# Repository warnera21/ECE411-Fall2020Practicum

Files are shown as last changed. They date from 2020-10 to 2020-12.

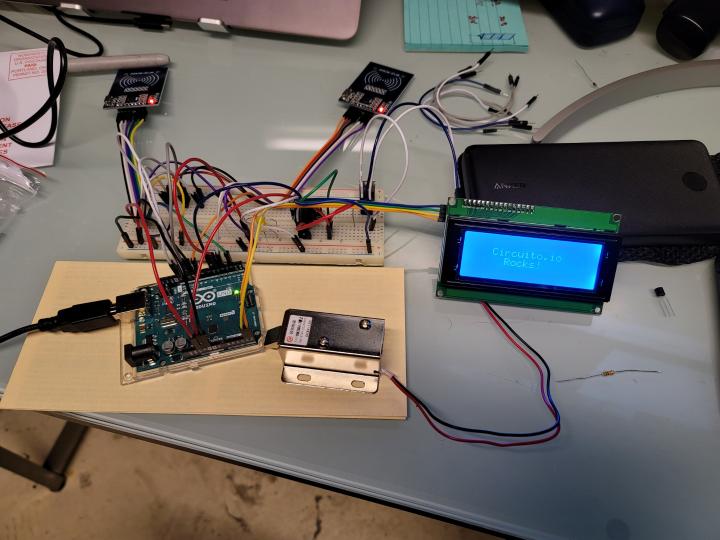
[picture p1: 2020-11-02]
Status Reports/Nov 2 2020 HW4 Picture.jpg

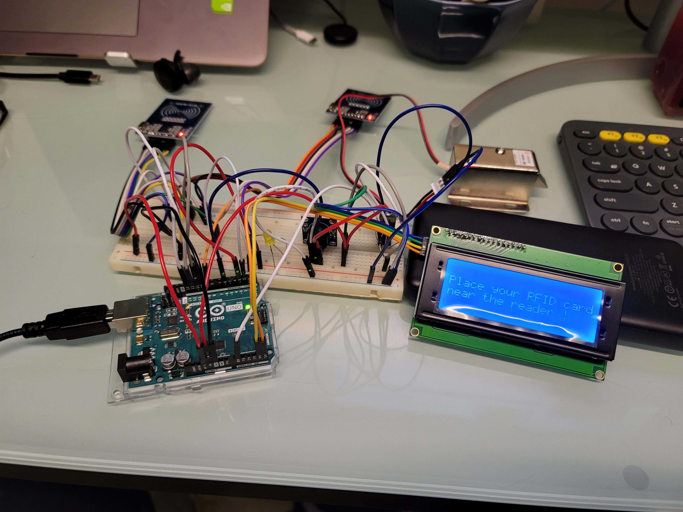
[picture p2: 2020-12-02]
breadboard- team 8.jpg

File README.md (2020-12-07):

# ECE411-Fall2020Practicum
This project is based in adding security and ease of access trough a door using Facial Recognition and RFID technologies. The implementation of keeping track of how many (Authorized) user go inside/out of a building is an extra feature that can aid with companies enforcing distancing strategies for COVID purposes. 

### TEAM 8: Hamed AlSaegui, Anthony Warner, Josh Pradera and Tamar Stigler-Flores.

### Arduino Code

	==> if the code is not uploaded yet
		the file (411.ino) must be inside a folder named (411)
		Follow the ... for board connections
		compile and upload the programm to the ATMega chip.
		
	==> used libraries
		SPI.h
		MFRC522.h
		LiquidCrystal_I2C.h
		Wire.h
	==> High Level Diagram Code
		set the LCD address to 0x27 for a 16 chars and 2 line display
		initialize the lcd
		initialize counter
		initialize receiveEvent function
			receive byte as a character
		VOID SETUP
			Initiate I2C communication
			Initiate  address bus designated to I2C with Raspberry Pi
			Initiate each MFRC522 card
			Join I2C bus as slave with address 8
				Call receiveEvent when data received 
			initialize output pins
		VOID LOOP
			be ready to scan a tag
				if scanned to ENTER (RFID1)
					If Tag is Valid
						AUTHORIZED
					If Tag is Not Valid
						UNAUTHORIZED
				if scanned to EXIT (RFID2)
					If Tag is Valid
						AUTHORIZED
					If Tag is Not Valid
						UNAUTHORIZED

### Raspberry Pi Code (Python Script)

	==> The sequence of the Face Recognition code goes as follow:
		1 - Collect the data set of pictures from each user.
		==> Used libraries: 
		    cv2 (openCV)
		    numpy
		 ==> Use the CascadeClassifier and load haarcascade_frontal_default.xml (used for the detection of faces)
		     Setup the raspberry pi camera
		     Setup input variable to assign an specific User ID (as a number)
		     WHILE TRUE
		     		Read from the raspberry pi camera.
				Set a onvertion for the photos from RGB to Gray Scale.
				Detect the face from the user.
				Increase the sampleNum variable by 1 as the picture samples are taken.
				Open window with video feed and also draw a rectangle on the detected face.
				Save 20 pictures in a folder named dataSet.
				When done break the LOOP.
		    Release the camera.
		    Destroy all the windows opened by the program.
		    
		    2- Train the data and create a file named trainingData.yml that will be used to recognize an user.
		       The .yml file contains  the serialized data for specific users.
		   ==> Used libraries:
		       os 
		       cv2
		       numpy
		       from PIL import Image (for manipulation of Images)
		       Create variable recognizer and call the function to create a Local Binary Operator.
		       	-  LBPH is used to extract features from an input image and match them with the faces in system's database.
		       Set the dataSet path.
		       Create  two arrays. One name faces and another names IDs.
		      		 Execute a for loop that will loop as many times as the amount of images that we have in the dataSet folder.
		      		 Convert images in monochromo format.
		      		 Convert images into a numpy array with name faceImg.
		      		 Extract ID from the name of the image and add it to the array IDs and add the data to the array faces.
		       Train the data set.
		       Save the .yml file inside recognizer folder.
		       Destroy all the windows opened by the program.
		       
		    3- Recognize a face an open the door.
		    ==> Used libraries:
		        numpy
			cv2
			time
			from smbus import SMBus (I2C communication)
		        Specify bus address used for I2C.
			Setup the CascadeClassifier function with the haarcascade_frontalface_default.xml
			Setup Raspberry Pi camera.
			Create a variable named rec and use the Local Binary Operator function.
			Load the trained data present in the .yml file.
			Initiate id to 0
			Create a solenoid function for the I2C communication between Raspberry Pi and Arduino.
				Write a byte 0x1 using bus address 0x8 to unlock the door.
				Wait for 5 seconds.
				Write a byte 0x0 using the same bus address  to Lock the door.
				
			While True
				Read from Raspberry Pi camera.
				Convert pictures from Color to Gray Scale.
				Set a Multiscale to compensate from faces closer and far away from the camera.
			        For LOOP 
					Start the prediction of the user based in the trained data and the face detected using the haar cascade file.
					Compare faces detected to IDs .
					If the ID and face detected match, release the camera and set the camera again for stability issues with the time library.
						Print the user Name in the terminal for testing purposes.
						Call the solenoid function and send  a 0x1 bit to the Arduino over I2C to unlock door.
						Wait for 5 seconds. 
						Send  a 0x0 bit to the Arduino to lock the door.
					ELSE IF ID dosnt match the trained data set.
						Print Unauthorized user in the terminal for testing purposes.
						Release the camera.
						Setup the camera. 
						
				Brake out of the program with cntrl+C. 
				Release the camera.
				Destroy all the windows created by the program.

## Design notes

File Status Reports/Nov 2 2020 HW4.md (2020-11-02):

Status Report - Nov 2 2020

Our breadboard is running one RFID reader correctly to read and verify the RFID Cards. The I2C LCD is connected and displays the
correct output to the user when "Access Denied" or "Authorized access." We have a yellow LED to also be another verification for the 
user to know if they are granted access. For now, we are having some issues with the second RFID reader and need to get the correct 
power supply for the solenoid to work with the breadboard setup.

A video of our breadboard working is on youtube at this link [RFID and Facial Recognition](https://youtu.be/yJKnMJHlXBU)

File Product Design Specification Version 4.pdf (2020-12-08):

12/07/2020 | Version 4

ECE411
Product Design Specifications PDS

### Facial Recognition Smart Door Lock

TEAM #8
Tamarr Stigler
Hamed AlSaeghi
Josh Pradera
Anthony Warner

12/06/2020 | Version 3

Introduction

This project consists of a Facial Recognition Smart Door Lock using RFID and Facial Recognition technology. RFID is known as the radio frequency identification, using electromagnetic fields to automatically identify tags that can be placed in many things. A part of this project is to use RFID cards to grant access to users entering and exiting a door. The system can also help in tracking the number of people existing inside the place as well as updating itself as users exit a door. There will be two sets of LEDs, a pair for the entrance signifying granted access and denied access and another set for the exiting also to communicate granted or unauthorized exit. The reason we want to grant authorized and unauthorized exiting is because the system will keep track of how many people in the building remain from the RFID door lock. There will be an LCD display that will show “Authorized Access!” when the user is recognized either by the face detection mode or by using the RFID , “Unauthorized access!” only when using the wrong RFID card.
In the case of the facial recognition section a user that is unauthorized to access will not trigger the opening of the door . Another part of the project is the use of Facial recognition from the user. We will be using a camera connected to a raspberry pi with the addition of openCV. The raspberry pi will communicate with the Atmega328 board via I2C (SDA and SCL pins) allowing the Atmega328 to trigger a solenoid lock and granting access to the user. It needs to recognize your face for approval. The objective of this project is to access a door having two options RFID and Facial Recognition. This system adds a layer of security to a door lock that can be implemented in any place, that be for the ease to enter a place without a key or for the added security introduced with RFID and Facial recognition.

Needs Statement

- A Facial Recognition Smart Door Lock is needed to provide users with more secure access to their properties.

Objectives Statement

- The objective of this project is to design and prototype a device that will make accessing properties safer by providing two authentication methods to unlock a door.

Market Analysis

This is intended towards any customers. We want to ensure it is useful for any security purposes. One way it could be used would be for homeland security. Another way it could be used is Business companies or corporations. Any Revences could use this as well.

Good ideas come with good competition. Common things facial recognition are used for are cellular phones and tablets. Currently Samsung and Iphones installed facial recognition for users and they used it as an authentication method to get permission. Same for some basic locks that follow the same methodology to provide access to a property. However, our product for the smart door will be providing much safer access to a property; it will not only scan your face, it also uses the tags scanning method as another authentication step with the potential of having it count the number of people entering and leaving with timings and push to a server to analyze it. We are planning to sell this product at $399.99. This price covers a profit since the value has been doubled.

Requirements

MUST
- Take a face as an input.
- Take an ID Tag as another input .
- Output for opening or not-opening the door.
- Has a visual interface for the user.
- Has at least 5 seconds between each output.
- Safe to use by non-engineers.
- Consistently recognize a face.
- Has an indicators to indicate access authorized/denied

SHOULD
- Not use batteries.
- Cost less than $300 to design.
- Always be running.
- Has two input options for Entering.
- Has one input option for Exiting.

MAY
- Has an interface with more than one language.
- Be able to do some statistical analysis.
- Be able to push statistics to a server and analyze it.
- Be able to register new users.

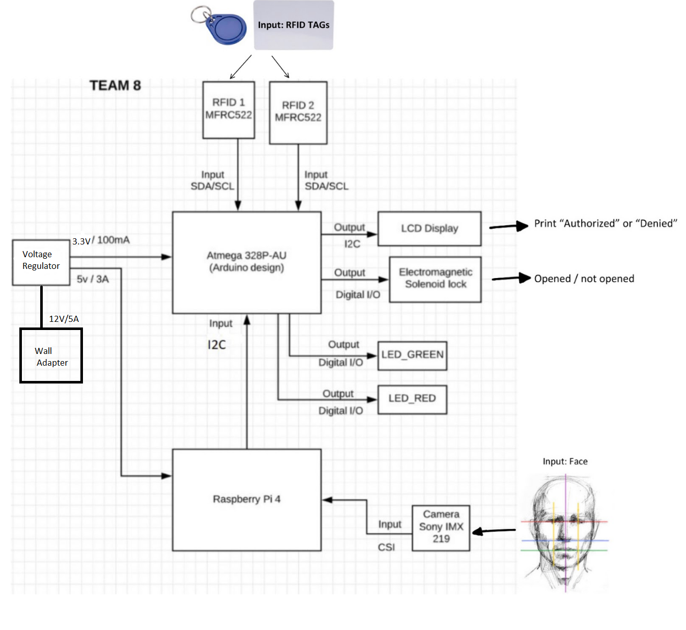
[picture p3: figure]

Design Specifications

- Raspberry PI 4 (4 GB).
- Atmega328-Au (Arduino Design).
- Wall adapter capable of 12V 5A.
- 6v 1.5A 11.4 mm Electromagnetic Solenoid Lock Assembly.
- Step up/down buck converter.
- Two RFID RC522 Module IC Car Reader Read RF Proximity Sensor.
- Raspberry Pi Noir Camera Module V2 8MP 1080p.
- LCD display Module 5v 20x4 Character LCM Blue Backlight.
- 2xRed Led and 2xGreen Led.
- Four 1kOhm resistors for the leds.
- Level Shifter.
- SD card.
- Stemedu RFID RC522 Module IC Card Reader Read RF Proximity Sensor ●

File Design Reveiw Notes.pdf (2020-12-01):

ECE411
PEER DESIGN REVIEW
TEAM 8

TEAM 8:
- Tamarr Stigler-Flores
- Anthony Warner
- Hamed AlSaeghi
- Josh Perdera

TEAM 16:
- Ahmad Alothaimin
- Nathan Paul
- Jakob White
- James Ross

SCHEMATIC NOTES:

- Remove supply diode.
- Remove 3.3v supply for raspberry pi
- Usbvcc will explode usb chip
- Diode OR connections (5v supply and usbvcc)
- DC plug connect to ground pins 2 and 3
- 4.7k pull-up 5v for LCD I2C
- 1k resistor for LEDs
- 100nF capacitor connection to gnd from USB shield
- Remove Q1 and R4
- S1 Switch:
Having (1 and 2) connecting in parallel and (3 and 4) in parallel. Isn’t this supposed to cause some issues ?
- Solenoid lock and other sensors:
Better to have them in separate blocks
- Having labels
Better to connect with wires rather than labels
- AREF
What is it? What does it do?

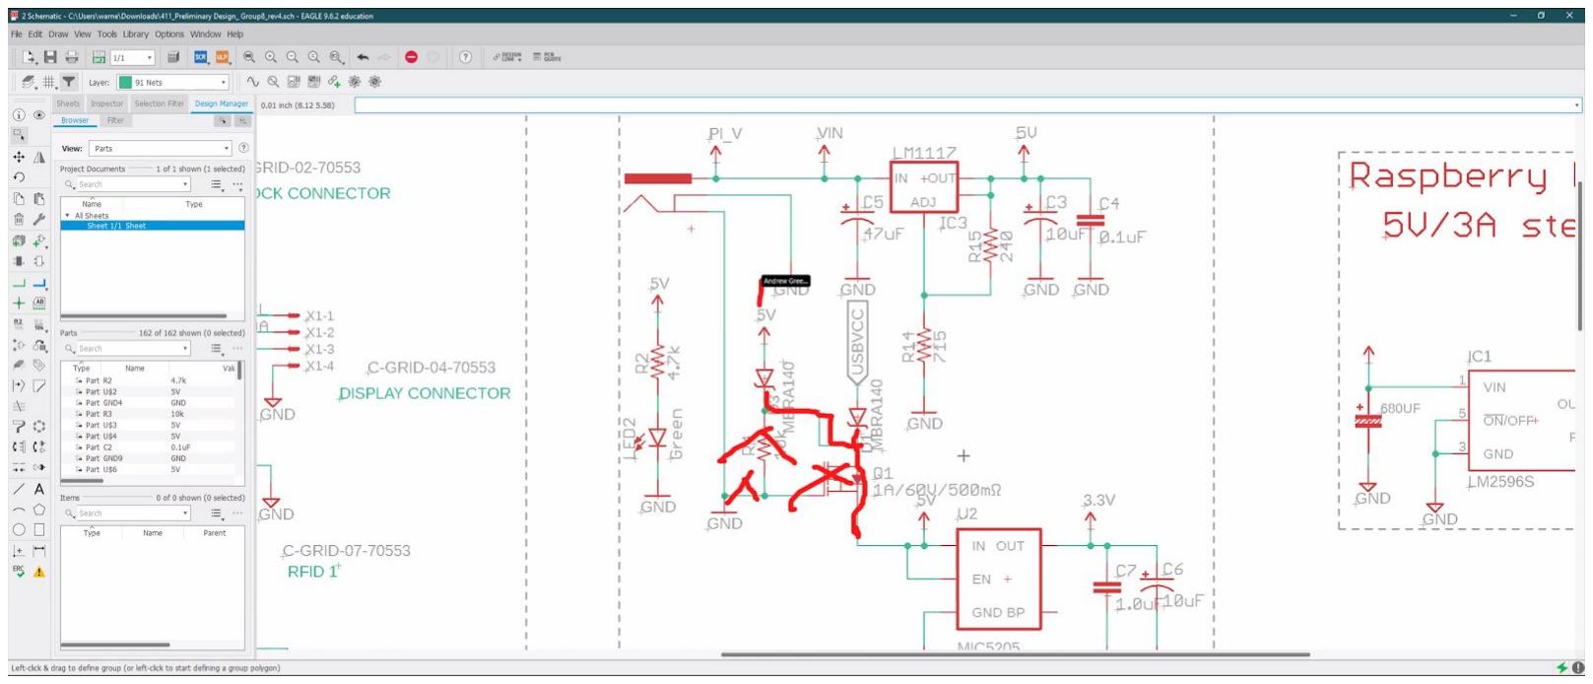
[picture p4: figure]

BOARD NOTES:

- More test points
- Gnd plane
- Test points
- Wider traces
- Board outline skewed
- Flood the gnd plane first
- Group switching power supply on board
- Thick lines on switching power supply
- Placement of mini usb
- Make the silk screen larger print
- Minimum trace size is 12mil for data lines and 50mil for power lines
- Add labels to test points
- Add more ground vias in open spaces

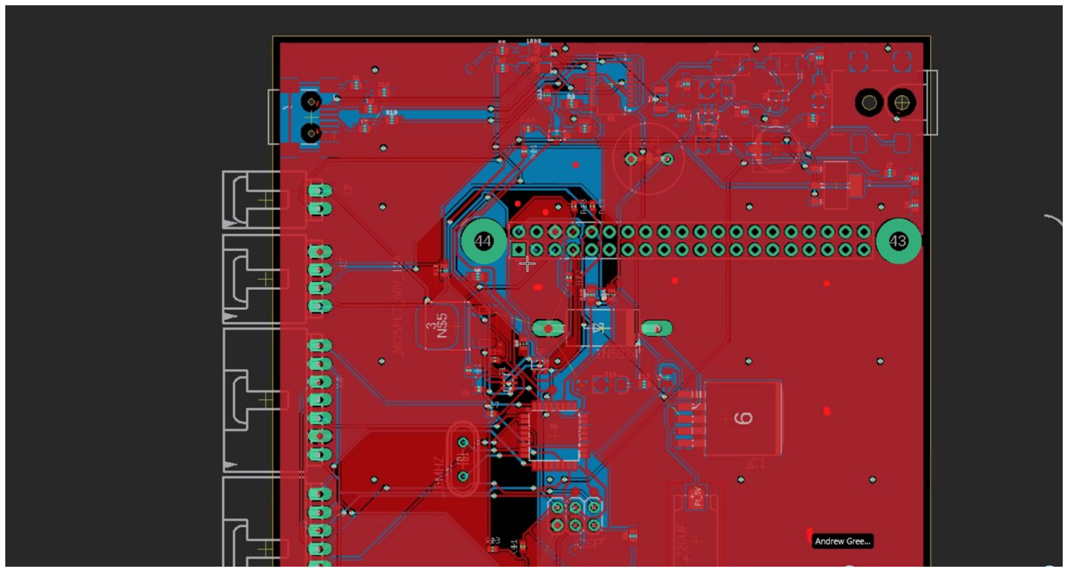
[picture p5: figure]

Big

g

e

r

S

M

D in

d

u

c

t

o

r

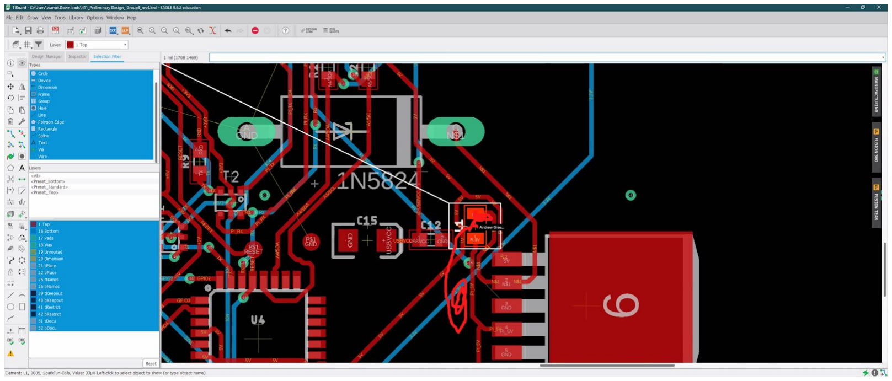
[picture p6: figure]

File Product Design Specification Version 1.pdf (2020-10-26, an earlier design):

10/25/2020 | Version 1

Tamarr Stigler
Hamed AlSaeghi
Josh Pradera
Anthony Warner
Team 8: Ultimate Alliance

Project: Facial Recognition Smart Door Lock

This project that we will be demonstrating is a Facial Recognition Smart Door Lock. The specific door lock that is proposed is the RFID Door Lock. RFID is known as the radio frequency identification, having the ability to track tags off of any given object. A part of this project is to use RFID cards to track users entering and exiting the door in order to test individuals performances and know the number of people existing inside the place. There will be one red led for decline access and one green led to show granted access along with an LCD display that will show granted or declined access. Another part of the project is the use of Facial recognition from the user. We will be using a camera sensor connected to a raspberry pi with the addition of openCV. The raspberry pi will communicate with the Atmega328 board via the RX/TX pins allowing the Atmega328 to trigger a solenoid lock and granting access to the user. It needs to recognize your face for approval. The objective of this project is to secure an access door with RFID and Facial Recognition and monitor its use. It’s important to have people safe from their surroundings. It will ensure the safety of any visitors. This has the capability towards all human users.

This is intended towards any customers. We want to ensure it is useful for any security purposes. One way it could be used would be for homeland security. Another way it could be used is Business companies or corporations. Any Revences could use this as well.

With all good ideas comes with good competition. Common things facial recognition are used for are cellular phones and tablets. Currently Samsung and Iphones installed facial recognition for users. Our product for the smart door will account when users are in and out. It counts the repetition on how many times you visited. It will log in the time when the entered and exit door. The RFID card is another tool for us to extend to new users. We are planning to sell this product at $399.99. This price covers a profit since the value has been doubled.

Requirements
Must
- Must use one RFID as a first authentication step to open the door.
- Must use Serial communication between Atmega328 and Raspberry Pi
- Must be able to recognize the person coming in via the facial recognition feature as a second authentication step to open the door.
- Must use Battery Pack to power the system
- Must be housed in an enclosure to be secured on a door
- Must use a Master card to edit users in the system

Should
- Should be able to communicate with the user via a 2X16 LCD screen.
- Should be able to use Green and Red LEDs to communicate “access granted” and “access denied”
- Should be able to be powered on for a week from the Battery Pack

May
- May use a second RFID to keep track of how many times people come in and leave the place, and how many are there inside the place.

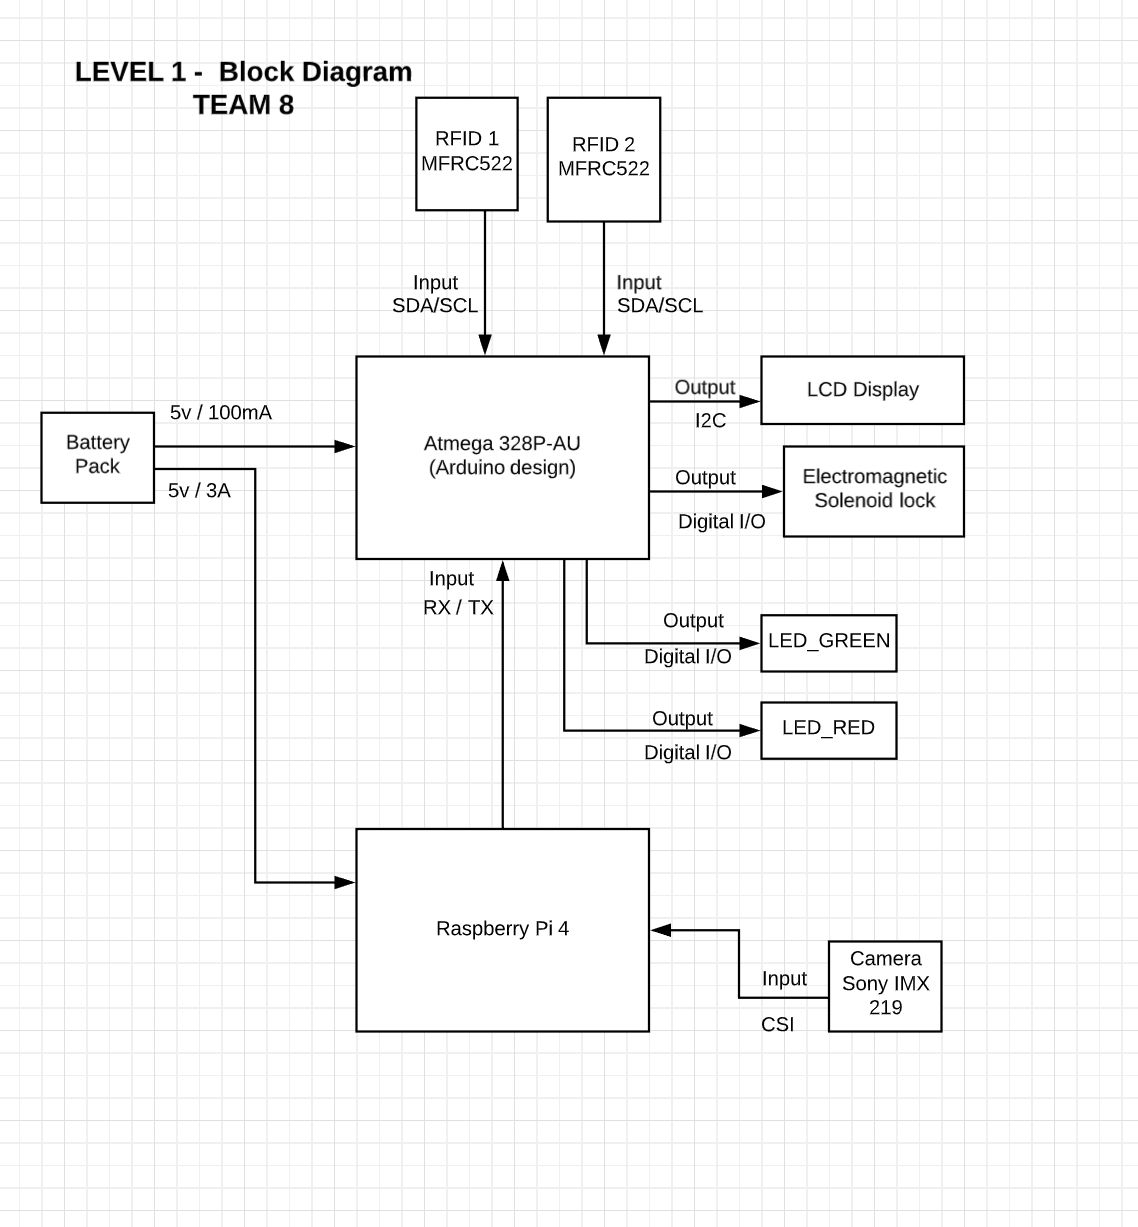
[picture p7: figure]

Design Specifications

- Raspberry PI
- Atmega328-Au (Arduino Design)
- Anker 20,000 mAh battery bank
- 6v 1.5A 11.4 mm Electromagnetic Solenoid Lock Assembly
- Step up/down buck converter
- Two RFID RC522 Module IC Car Reader Read RF Proximity Sensor
- Raspberry Pi Noir Camera Module V2 8MP 1080p
- LCD display Module 5v 16x2 Character LCM Blue Backlight
- 1xRed Led and 1xGreen Led
- SD cards

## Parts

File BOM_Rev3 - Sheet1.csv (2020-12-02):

Qty | Value | Device | Package | Parts | Description | MANUFACTURER | MPN | Vendor
1 | - | CONN_02 | 1X02 | J1 | PIN HEADER, VERTICAL, NON-SHROUD | METZ CONNECT USA Inc. | 31027102 | Digikey
1 | - | CONN_06SILK_FEMALE_PTH | 1X06 | J5 | PIN HEADER, VERTICAL, NON-SHROUD | TE Connectivity / AMP | 31027106 | Digikey
2 | - | CONN_08",1X08" | 2x08 | J2, J4 | PIN HEADER, VERTICAL, NON-SHROUD | METZ CONNECT USA Inc. | 826629-8 | Mouser
1 | - | LED5MM | LED5MM | GREEN1 | LED LED SINGLE 5MM GREEN DIFFUSED | QT Brightek (QTB) | QBL8YG60D-MP7 | Digikey | Digikey Alt.
1 | - | LED5MM | LED5MM | RED1 | LED LED SINGLE 5MM RED DIFFUSED | QT Brightek (QTB) | QBL8SA60D-MP7 | Digikey | Digikey Alt.
1 | 5A | SCHOTTKY-DIODECB429-15 | CB429-15 through hole | 1N5824 | Schottky Diode DIODE SCHOTTKY 5A 30V TOPHAT, diameter 5 mm, horizontal, grid 15.24 mm | Microsemi Corporation | 1N5824 | Digikey
1 | 0.1uF | 0.1UF- Capacitor | Generic 1608 (0603) package | C2 | Multilayer Ceramic Capacitors MLCC - SMD/SMT 50V .1uF X7R 0603 10% AEC-Q200 | KEMET | C0603C104K5RAC3121 | Mouser
1 | 1.0uF | 1.0UF-0603-16V-10% | Generic 1608 (0603) package | C7 | Multilayer Ceramic Capacitors MLCC - SMD/SMT 16volts 1uF X7R 10% | KEMET | C0603C105K4RAC7411 | Mouser
1 | 10KOhm | R-US_M1406 | M1406 | R5 | RES 10K OHM 0.1% 2/5W 2010 | Vishay Dale | MCA12060C1002FP500 | Digikey
1 | 10kOhm | RES SMD 10K OHM 5% 1/10W 0603 | Generic 1608 (0603) | R3 | 10 kOhms ±5% 0.1W, 1/10W Chip Resistor 0603 (1608 Metric) Thick Film | Yageo | RC0603JR-0710KL | DigiKey
1 | 10uF | 10UF-POLAR-EIA3216-16V-10%(TANT) | EIA 3216 (1206) | C6 | 10µF Molded Tantalum Capacitors 16V 1206 (3216 Metric) 1.7Ohm | Vishay Sprague | TR3A106K016C1700 | DigiKey
1 | 16MHZ | CRYSTALHC49S | HC49/S | 16MHZ | 16.000312MHz ±30ppm Crystal 18pF 40 Ohms HC-49/US | ECS Inc. | ECS-160.003-18-4 | DigiKey
4 | 1KOhm | RES SMD 1K OHM 1% 1/20W 0502 | 0502 (1406 Metric) | R4, R14, R15, R24 | 1 kOhms ±1% 0.05W, 1/20W Chip Resistor 0502 (1406 Metric) Military, Non-Inductive Thin Film | Vishay Dale | M55342H01B1E00RWS | Digikey
1 | 1 MOhm | 1 MOhm resistor | Generic 1608 (0603) | R1 | Thick Film Resistors - SMD 1M OHM 1% 1/4W TC100 | Bourns | CMP0603-FX-1004ELF | Mouser
1 | 1N4001-TP | 1N4004 | DO-204AL, DO-41, Axial | D2 | Diode Standard 400V 1A Through Hole DO-41 | NTE Electronics, Inc | 1N4004-T | Mouser
2 | 20pF | 20pF capacitor SMD | Generic 1608 (0603) | C3, C4 | Multilayer Ceramic Capacitors MLCC - SMD/SMT 100V 20pF C0G 0603 1% | KEMET | CBR06C200F1GAC | Mouser
1 | 220uF | 220uF capacitor SMD | 139CLL | C5 | CAP ALUM 220UF 20% 6.3V SMD | Vishay | MAL213963221E3 | Digikey
1 | 33uH | 33uH inductor | 4.9 mm x 4.9 mm x 2 mm | L2 | Fixed Inductors 33uH 0.43A 160ohms | Sumida | CDPH4D19FNP-330MC | Mouser | Digikey Alt.
3 | 4.7k | 4.7KOHM-0603-1/10W-1% | 603 | R2, R25, R26 | 4.7kΩ resistor | Pansonic | ERA-3VEB4701V | Mouser
4 | 4k7 | RESISTOR-0402 | C0402 | R18, R19, R20, R21 | Resistors | Pansonic | ERA-2VEB4701X | Mouser
1 | 680uf | CPOL-US153CLV-0605 | 153CLV-0605 | C11 | POLARIZED CAPACITOR, American symbol | Vishay | MAL215363101E3 | Newark
1 | ATMEGA328P_TQFP | ATMEGA328P_TQFP | TQFP32-08 | U4 | Popular 328P in QFP | MicroChip | ATMEGA328P-AU | Mouser | ATMEGA328P-AUR Microchip Technology | Integrated Circuits (ICs) | DigiKey
1 | BSS138PS | BSS138PS | SOT363 | T2 | BSS138 Dual N-Channel MOSFET (UGS +/-20V, RDS 1Ohm, ID 320mA) | Nexperia | BSS138PS,115 | Mouser
1 | C-GRID-02-70553 | C-GRID-02-70553 | 70553-02 | X2 | CONNECTOR | Molex | 70553-0036 | Digikey Male | Female
1 | C-GRID-04-70553 | C-GRID-04-70553 | 70553-04 | X1 | CONNECTOR | Molex | 70553-0107 | Digikey male | Female
1 | C-GRID-07-70553 | C-GRID-07-70553 | 70553-07 | X4 | CONNECTOR | Molex | 70553-0036 | Digikey 3pos Male | 3pos Female
1 | C-GRID-09-70553 | C-GRID-09-70553 | 70553-09 | X6 | CONNECTOR | Molex | 70553-0036 | Digikey 3pos Male | 3pos Female
6 | Green | LED1206 | LED-1206 | LED2 | LED GREEN CLEAR CHIP SMD | Kingbright | APT3216CGCK | Digikey
1 | ICSP | PINHD-2X3 | 2X03 | ICSP | PIN HEADER
1 | LM2596S | LM2596S | TO263-5 | IC1 | SIMPLE SWITCHER® Power Converter 150 kHz 3A Step-Down Voltage Regulator | LM2596SX-5.0/NOPB | LM2596S-ADJ/NOPB | Digikey
1 | MIC5205 | MIC52053.3V | SOT23-5 | U2 | IC REG LINEAR 3.3V 150MA SOT23-5 | Microchip Technology | MIC5205-3.3YM5-TR | Digikey
1 | NTD3055L104G | NTD3055L104G | DPAK3 | MOSFET_60V_12A | 12 A, 60 V, Logic Level N−Channel | ON SEMICONDUCTOR | NTD3055L104G | Mouser
1 | POWER_JACKSUPER_BOMB_DIGITY | POWER_JACKSUPER_BOMB_DIGITY | POWER_JACK_SMD_OVERPASTE_SUPER_BOMB_DIGITY | J3 | Power Jack | ADAM TECH | ADC-028-2 | Sparkfun
1 | RASPI_BOARD_B+_E4P | RASPI_BOARD_B+_E4P | RASPI_BOARD_B+_EDGES_4DRILL_PAD | X5 | Adafruit Accessories GPIO Header for Raspberry Pi A+/B+/Pi 2/Pi 3/Pi 4/Zero - 2x20 Female Header | Adafruit | 2222 | Mouser
1 | RESET | SWITCH_SPST_4_PINSQUARE | TACTILE-SWITCH-SMD | S1 | Tactile Switch SPST-NO Top Actuated Surface Mount | TE Connectivity ALCOSWITCH Switches | FSM6JSMATR | Digikey
13 | TP-3x5 | TEST-POINT3X5 | PAD.03X.05 | TP1, TP2, TP3, TP4, TP5, TP6, TP7, TP8, TP10, TP11, TP12, TP15, TP16 | SparkFun Test Points | - | - | -

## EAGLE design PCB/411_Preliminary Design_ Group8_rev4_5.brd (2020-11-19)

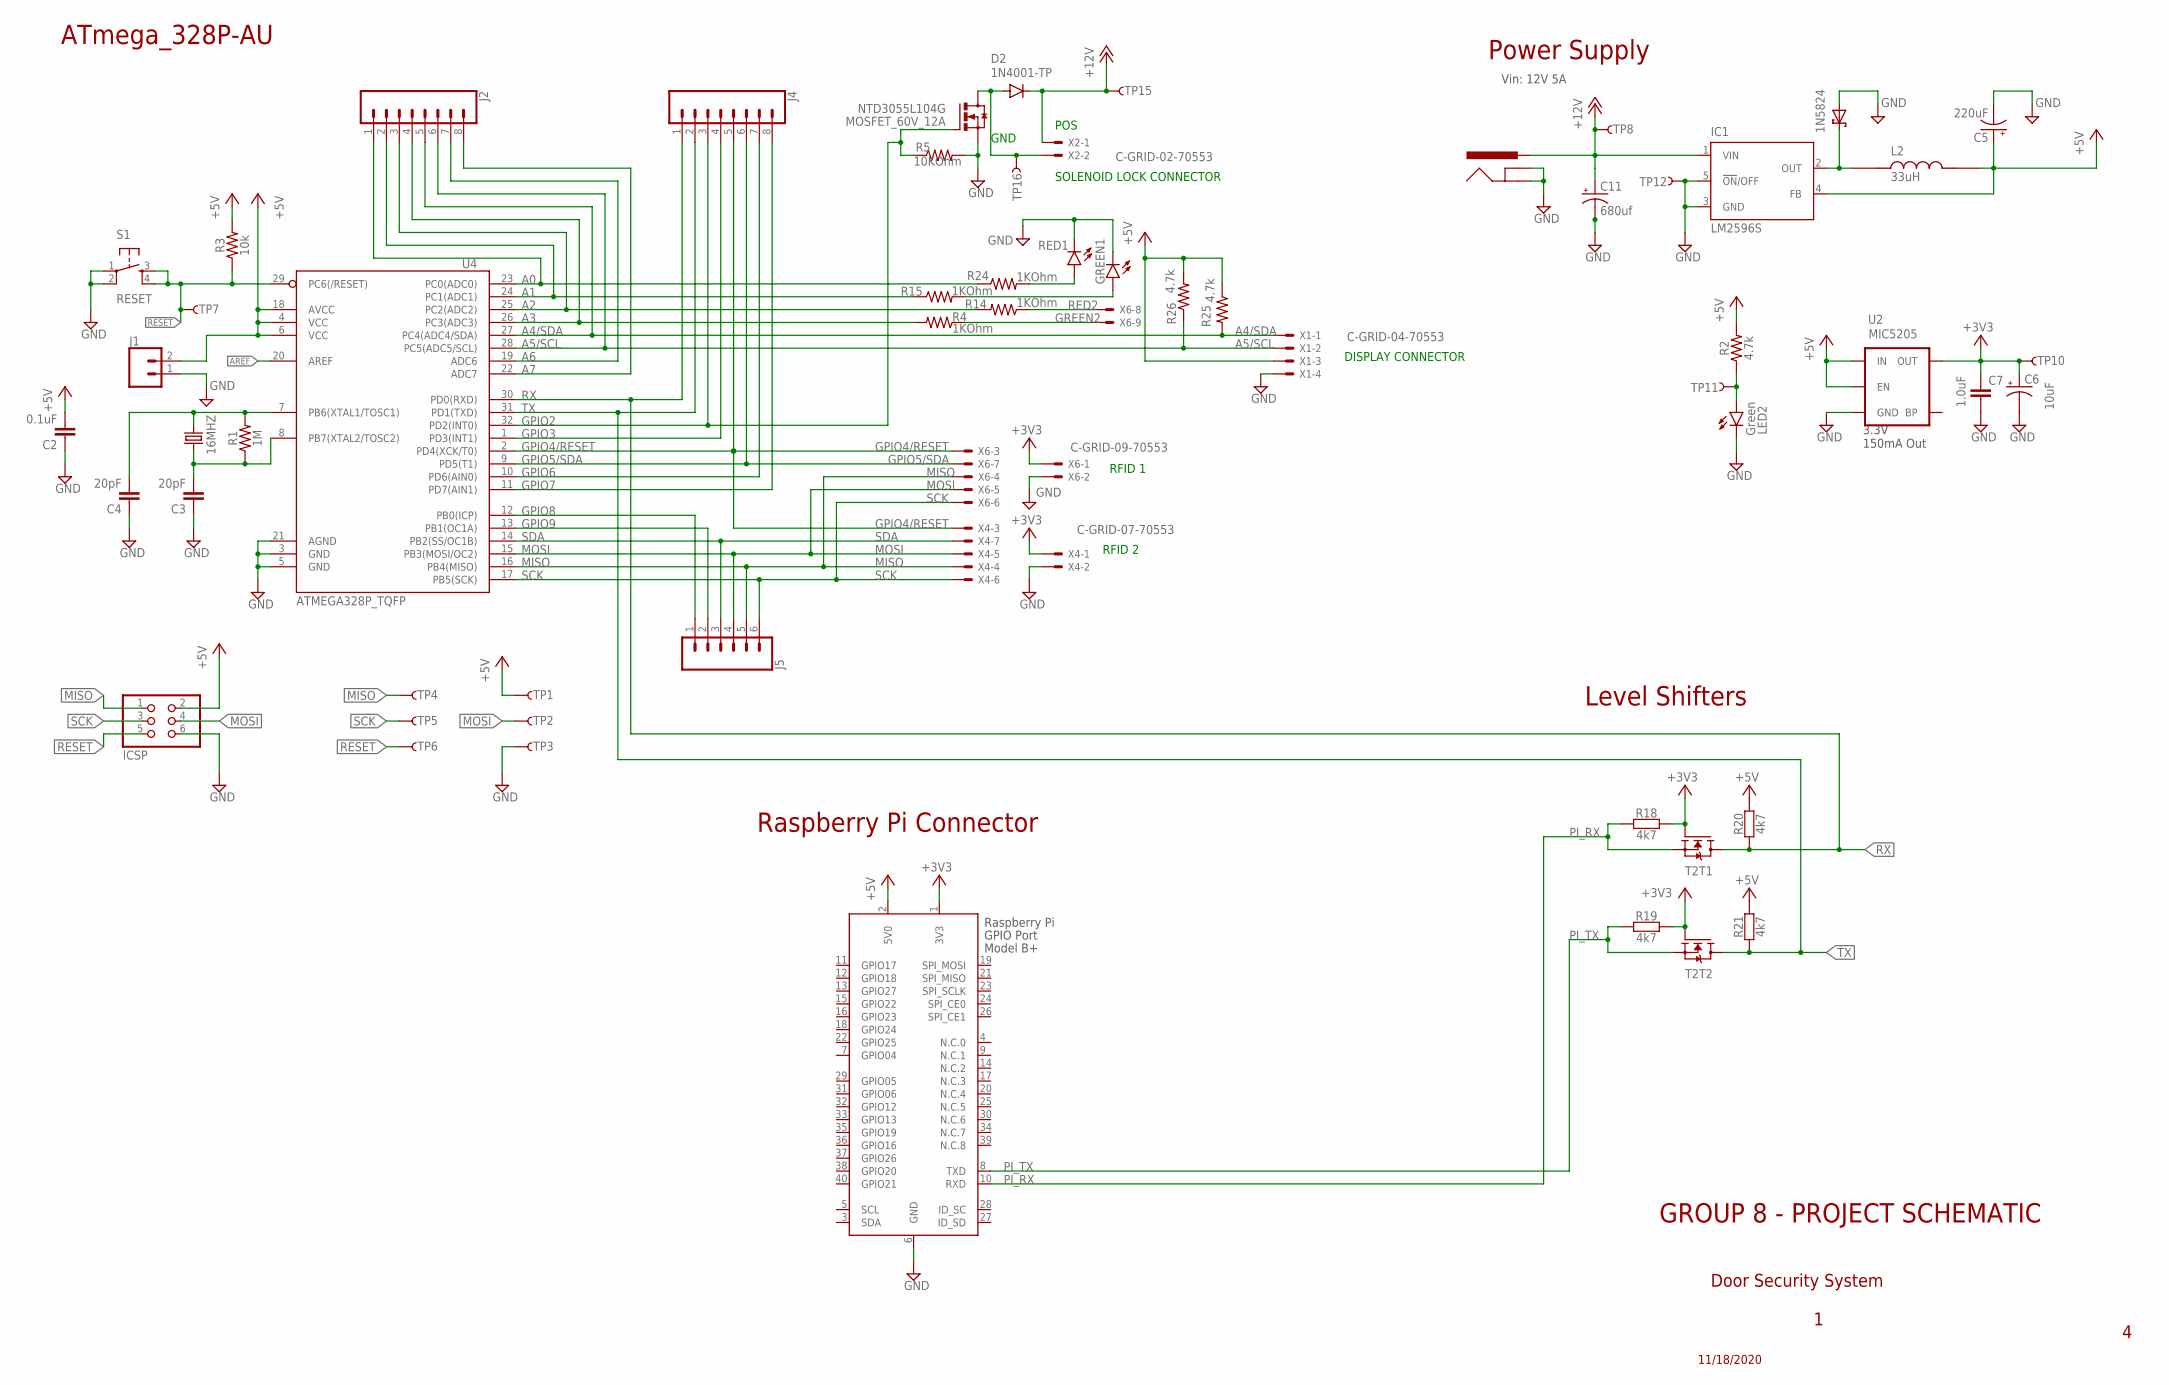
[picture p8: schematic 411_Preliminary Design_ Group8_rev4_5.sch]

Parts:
1N5824: SCHOTTKY-DIODECB429-15; CB429-15
16MHZ: 16MHZ; HC49/S
C2: 0.1uF; 0603
C3, C4: 20pF; 0603
C5: 220uF; 153CLV-0605
C6: 10uF; EIA3216
C7: 1.0uF; 0603
C11: 680uf; 153CLV-0605
D2: 1N4001-TP; DO41-10
GREEN1: LED5MM
IC1: LM2596S; TO263-5
ICSP: ICSP; 2X03
J1: CONN_02; 1X02
J2, J4: CONN_08"; 1X08
J3: POWER_JACKSUPER_BOMB_DIGITY; POWER_JACK_SMD_OVERPASTE_SUPER_BOMB_DIGITY
J5: CONN_06SILK_FEMALE_PTH; 1X06
L2: 33uH; IND_#B953AS-330M=P3
LED2: Green; LED-1206
MOSFET_60V_12A: NTD3055L104G; DPAK3
R1: 1M; 0603
R2, R25, R26: 4.7k; 0603
R3: 10k; 0603
R4, R14, R15, R24: 1KOhm; M1406
R5: 10KOhm; M1406
R18, R19, R20, R21: 4k7; C0402
RED1: LED5MM
S1: RESET; TACTILE-SWITCH-SMD
T2: BSS138PS; SOT363
TP1, TP2, TP3, TP4, TP5, TP6, TP7, TP8, TP10, TP11, TP12, TP15, TP16: TP-3x5; PAD.03X.05
U2: MIC5205; SOT23-5
U4: ATMEGA328P_TQFP; TQFP32-08
X1: C-GRID-04-70553; 70553-04
X2: C-GRID-02-70553; 70553-02
X4: C-GRID-07-70553; 70553-07
X5: RASPI_BOARD_B+_E4P; RASPI_BOARD_B+_EDGES_4DRILL_PAD
X6: C-GRID-09-70553; 70553-09

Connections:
+3V3: C6.+, C7.1, R18.2, R19.2, T2.2 (G), T2.5 (G), TP10.P$1, U2.5 (OUT), X4.1, X5.1 (3V3), X6.1
+5V: C2.2, C5.+, IC1.4 (FB), ICSP.2, J1.2, L2.2, R2.2, R3.2, R20.2, R21.2, R25.1, R26.2, TP1.P$1, U2.1 (IN), U2.3 (EN), U4.4 (VCC), U4.6 (VCC), U4.18 (AVCC), X1.3, X5.2 (5V0)
+12V: C11.+, D2.C, IC1.1 (VIN), J3.VIN0 (PWR), TP8.P$1, TP15.P$1, X2.1
A0: J2.1, R24.1, U4.23 (PC0(ADC0))
A1: J2.2, R15.1, U4.24 (PC1(ADC1))
A2: J2.3, R14.2, U4.25 (PC2(ADC2))
A3: J2.4, R4.2, U4.26 (PC3(ADC3))
A4/SDA: J2.5, R25.2, U4.27 (PC4(ADC4/SDA)), X1.1
A5/SCL: J2.6, R26.1, U4.28 (PC5(ADC5/SCL)), X1.2
A6: J2.7, U4.19 (ADC6)
A7: J2.8, U4.22 (ADC7)
AREF: U4.20 (AREF)
GND: 1N5824.A, C2.1, C3.1, C4.1, C5.-, C6.-, C7.2, C11.-, GREEN1.K (C), IC1.3 (GND), IC1.5 (!ON!/OFF), ICSP.6, J1.1, J3.GND (GNDBREAK), J3.P$4 (GND), LED2.C, MOSFET_60V_12A.2 (S), R5.2, RED1.K (C), S1.1, S1.2, TP3.P$1, TP12.P$1, U2.2 (GND), U4.3 (GND), U4.5 (GND), U4.21 (AGND), X1.4, X4.2, X5.6 (GND), X6.2
GPIO2: J4.3, MOSFET_60V_12A.1 (G), R5.1, U4.32 (PD2(INT0))
GPIO3: J4.4, U4.1 (PD3(INT1))
GPIO4/RESET: J4.5, U4.2 (PD4(XCK/T0)), X4.3, X6.3
GPIO5/SDA: J4.6, U4.9 (PD5(T1)), X6.7
GPIO6: J4.7, U4.10 (PD6(AIN0))
GPIO7: J4.8, U4.11 (PD7(AIN1))
GPIO8: J5.1, U4.12 (PB0(ICP))
GPIO9: J5.2, U4.13 (PB1(OC1A))
GREEN2: R4.1, X6.9
MISO: ICSP.1, J5.5, TP4.P$1, U4.16 (PB4(MISO)), X4.4, X6.4
MOSI: ICSP.4, J5.4, TP2.P$1, U4.15 (PB3(MOSI/OC2)), X4.5, X6.5
unnamed: 1N5824.C, IC1.2 (OUT), L2.1
unnamed: LED2.A, R2.1, TP11.P$1
unnamed: 16MHZ.2, C4.2, R1.2, U4.7 (PB6(XTAL1/TOSC1))
unnamed: 16MHZ.1, C3.2, R1.1, U4.8 (PB7(XTAL2/TOSC2))
unnamed: D2.A, MOSFET_60V_12A.3 (D), TP16.P$1, X2.2
unnamed: GREEN1.A, R15.2
unnamed: R24.2, RED1.A
PI_RX: R18.1, T2.1 (S), X5.10 (RXD)
PI_TX: R19.1, T2.4 (S), X5.8 (TXD)
RED2: R14.1, X6.8
RESET: ICSP.5, R3.1, S1.3, S1.4, TP6.P$1, TP7.P$1, U4.29 (PC6(/RESET))
RX: J4.1, R20.1, T2.6 (D), U4.30 (PD0(RXD))
SCK: ICSP.3, J5.6, TP5.P$1, U4.17 (PB5(SCK)), X4.6, X6.6
SDA: J5.3, U4.14 (PB2(SS/OC1B)), X4.7
TX: J4.2, R21.1, T2.3 (D), U4.31 (PD1(TXD))

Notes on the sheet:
ATmega_328P-AU
RFID 1
RFID 2
DISPLAY CONNECTOR
SOLENOID LOCK CONNECTOR
GND
POS
Door Security System
GROUP 8 - PROJECT SCHEMATIC
11/18/2020
Level Shifters
Power Supply
3.3V 150mA Out
Vin: 12V 5A
Raspberry Pi Connector

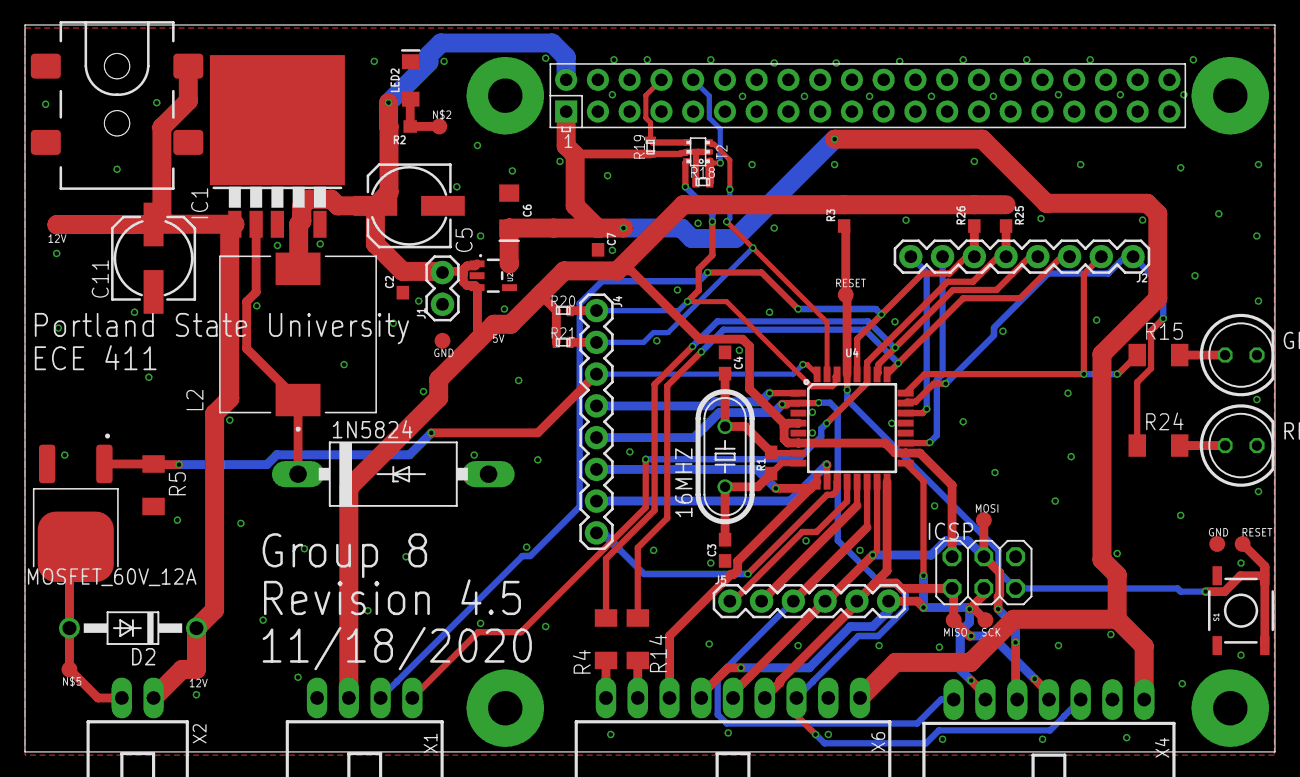
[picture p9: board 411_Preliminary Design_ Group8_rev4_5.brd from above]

Board: 2 copper layers, 100.0 x 58.2 mm, 58 parts (0 on the bottom side), 38 nets.

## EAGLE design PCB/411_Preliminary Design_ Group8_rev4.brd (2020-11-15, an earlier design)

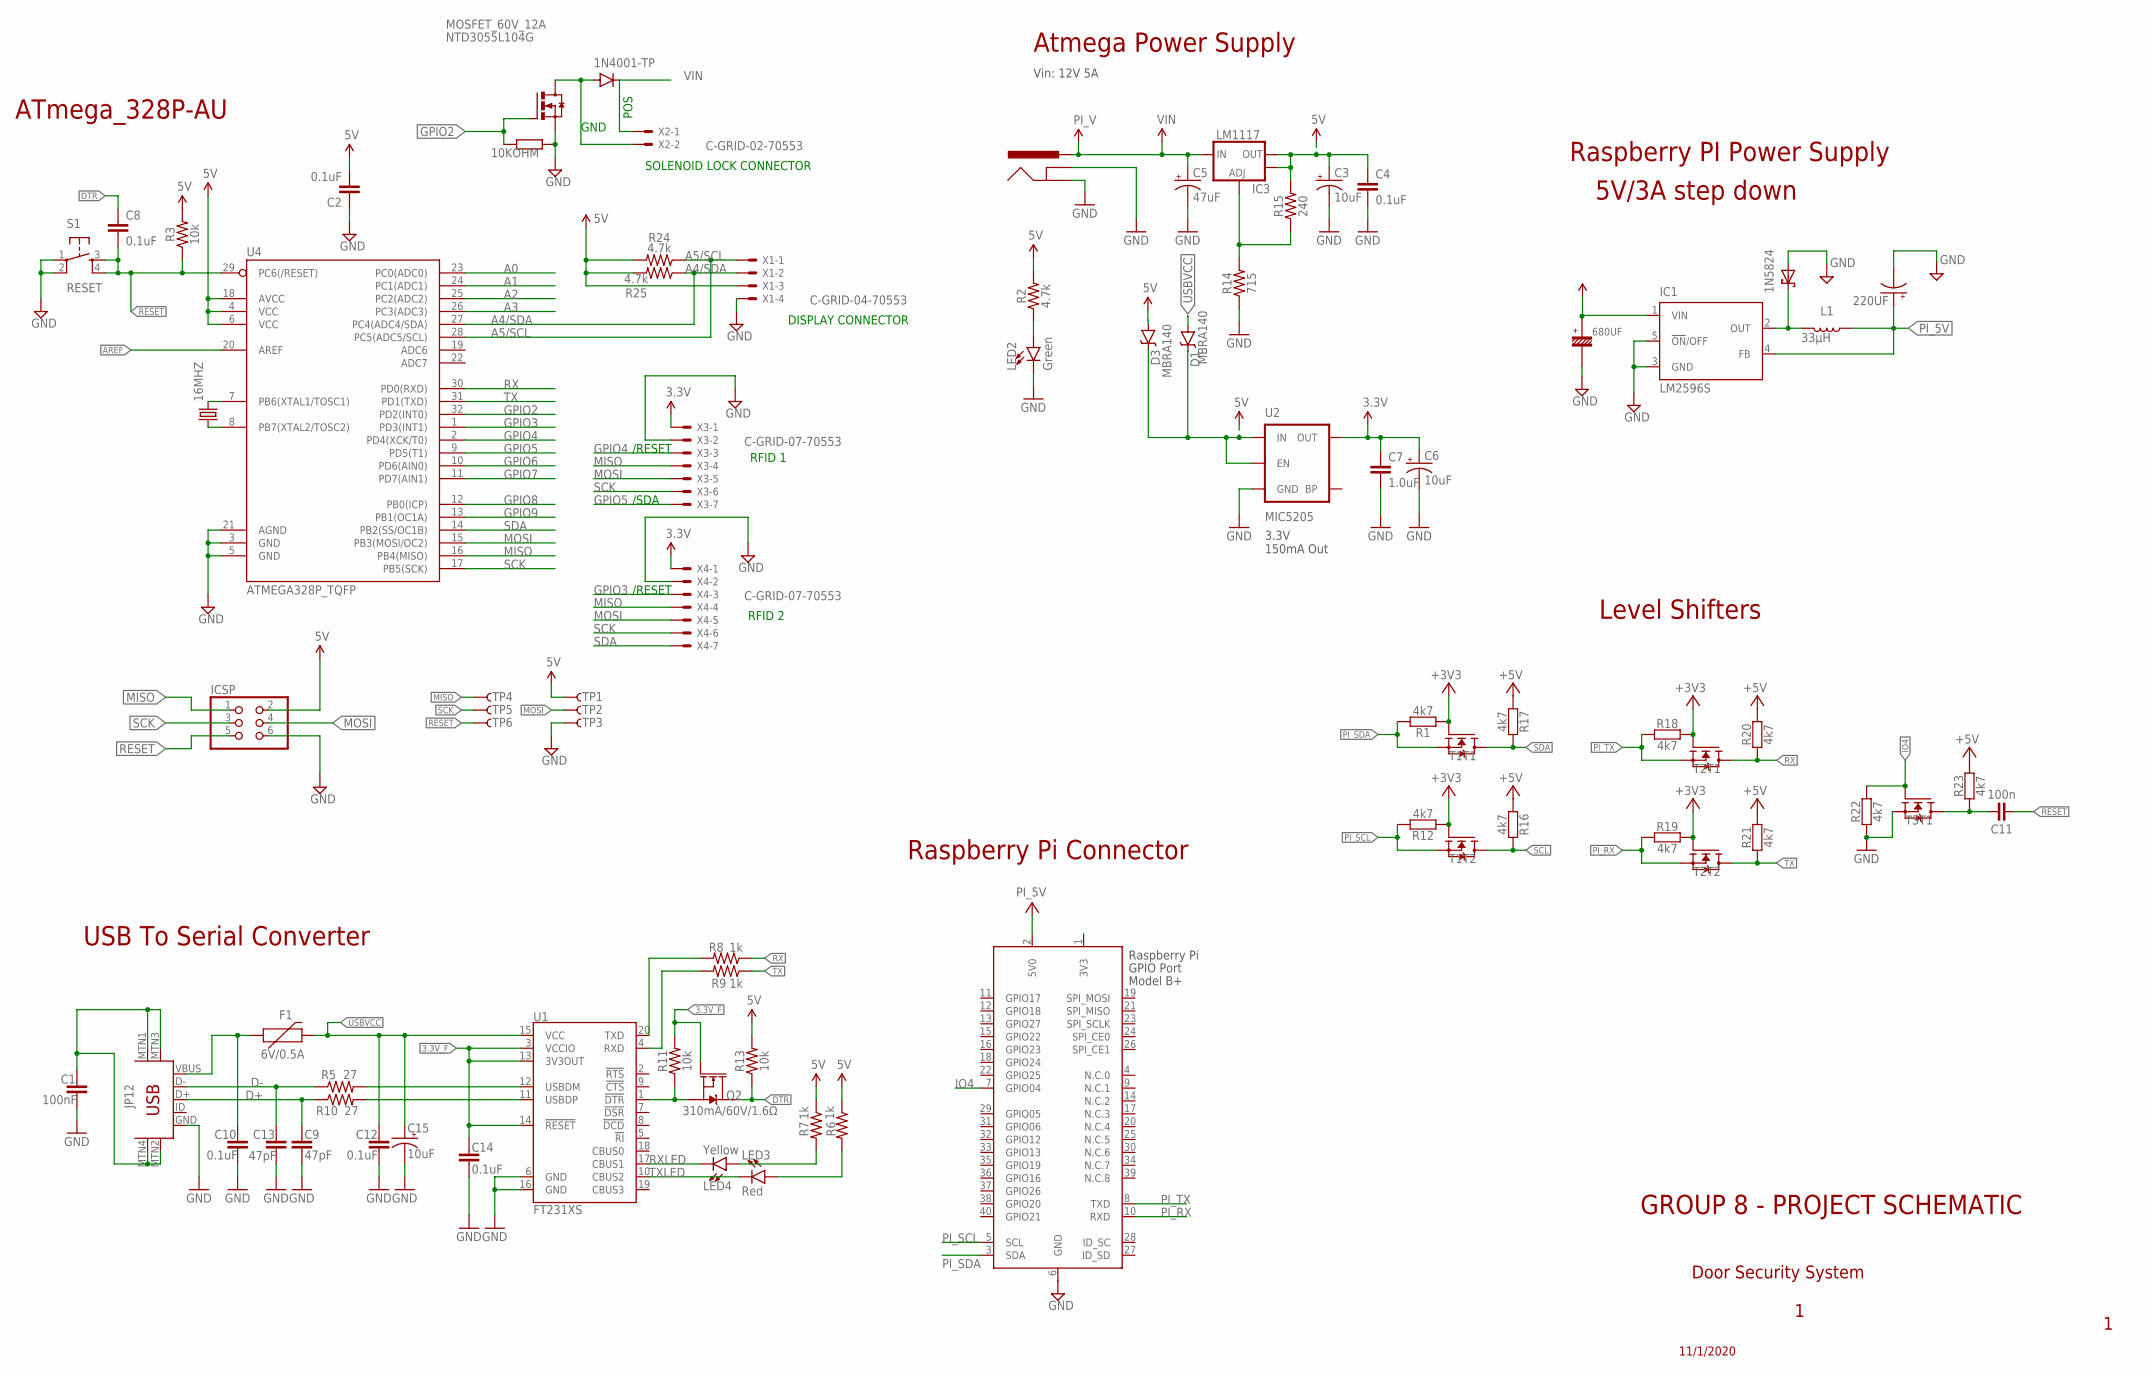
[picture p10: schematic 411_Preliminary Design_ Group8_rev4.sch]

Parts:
1N5824: SCHOTTKY-DIODECB429-15; CB429-15
16MHZ: CRYSTALHC49S; HC49/S
220UF: CPOL-US139CLL-2R; 139CLL-2R
680UF: CE-16V-10-5.08; 16V-10-5.08
C1: 100nF; 0603
C2, C4, C8, C10, C12, C14: 0.1uF; 0603
C3, C6, C15: 10uF; EIA3216
C5: 47uF; PANASONIC_D
C7: 1.0uF; 0603
C9, C13: 47pF; 0603
C11: 100n; C0402
D1, D3: MBRA140; SMA-DIODE
F1: 6V/0.5A; 1206
IC1: LM2596S; TO263-5
IC3: LM1117; SOT223-ALT1
ICSP: PINHD-2X3; 2X03
J3: POWER_JACKSUPER_BOMB_DIGITY; POWER_JACK_SMD_OVERPASTE_SUPER_BOMB_DIGITY
JP12: USB-MINIB-5PIN; USB-MINIB
L1: 33µH; 0805
LED2: Green; LED-1206
LED3: Red; LED-1206
LED4: Yellow; LED-1206
MOSFET_60V_12A: NTD3055L104G; DPAK3
Q2: 310mA/60V/1.6Ω; SOT323
R1, R12, R16, R17, R18, R19, R20, R21, R22, R23: 4k7; C0402
R2, R24, R25: 4.7k; 0603
R3, R11, R13: 10k; 0603
R5, R10: 27; 0603
R6, R7, R8, R9: 1k; 0603
R14: 715; 0603
R15: 240; 0603
S1: RESET; TACTILE-SWITCH-SMD
T1, T2, T3: BSS138PS; SOT363
TP1, TP2, TP3, TP4, TP5, TP6: TP-3x5; PAD.03X.05
U1: FT231XS; SSOP20_L
U2: MIC5205; SOT23-5
U4: ATMEGA328P_TQFP; TQFP32-08
X1: C-GRID-04-70553; 70553-04
X2: C-GRID-02-70553; 70553-02
X3, X4: C-GRID-07-70553; 70553-07
X5: RASPI_BOARD_B+_E4P; RASPI_BOARD_B+_EDGES_4DRILL_PAD

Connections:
3.3V: C6.+, C7.1, U2.5 (OUT), X3.1, X4.1
3.3V_F: C14.1, Q2.1 (G), R11.2, U1.3 (VCCIO), U1.13 (3V3OUT), U1.14 (!RESET)
3V3: X5.1 (3V3)
5V: 680UF.+, C2.2, C3.+, C4.1, D1.C, D3.A, D3.C, IC1.1 (VIN), IC3.2 (OUT), IC3.4 (OUT), ICSP.2, R2.2, R3.2, R6.1, R7.1, R13.2, R15.2, R24.2, R25.2, TP1.P$1, U2.1 (IN), U2.3 (EN), U4.4 (VCC), U4.6 (VCC), U4.18 (AVCC), X1.3
+3V3: R1.1, R12.1, R18.2, R19.2, T1.2 (G), T1.5 (G), T2.2 (G), T2.5 (G)
+5V: R16.1, R17.1, R20.2, R21.2, R23.2
A0: U4.23 (PC0(ADC0))
A1: U4.24 (PC1(ADC1))
A2: U4.25 (PC2(ADC2))
A3: U4.26 (PC3(ADC3))
A4/SDA: R25.1, U4.27 (PC4(ADC4/SDA)), X1.2
A5/SCL: R24.1, U4.28 (PC5(ADC5/SCL)), X1.1
AREF: U4.20 (AREF)
D0_RX1: C11.2, R23.1, T3.6 (D)
D+: C9.1, JP12.D+, R10.1
D-: C13.1, JP12.D-, R5.1
DTR: C8.1, Q2.3 (D), R13.1
FTDI_DTR: Q2.2 (S), R11.1, U1.1 (!DTR)
GND: 1N5824.A, 220UF.-, 680UF.-, C1.2, C2.1, C3.-, C4.2, C5.-, C6.-, C7.2, C9.2, C10.2, C12.2, C13.2, C14.2, C15.-, IC1.3 (GND), IC1.5 (!ON!/OFF), ICSP.6, J3.GND (GNDBREAK), J3.P$4 (GND), JP12.GND, LED2.C, MOSFET_60V_12A.2 (S), R14.1, R22.1, S1.1, S1.2, T3.1 (S), TP3.P$1, U1.6 (GND), U1.16 (GND), U2.2 (GND), U4.3 (GND), U4.5 (GND), U4.21 (AGND), X1.4, X3.2, X4.2, X5.6 (GND)
GPIO2: MOSFET_60V_12A.1 (G), U4.32 (PD2(INT0))
GPIO3: U4.1 (PD3(INT1)), X4.3
GPIO4: U4.2 (PD4(XCK/T0)), X3.3
GPIO5: U4.9 (PD5(T1)), X3.7
GPIO6: U4.10 (PD6(AIN0))
GPIO7: U4.11 (PD7(AIN1))
GPIO8: U4.12 (PB0(ICP))
GPIO9: U4.13 (PB1(OC1A))
IO4: R22.2, T3.2 (G), X5.7 (GPIO04)
MISO: ICSP.1, TP4.P$1, U4.16 (PB4(MISO)), X3.4, X4.4
MOSI: ICSP.4, TP2.P$1, U4.15 (PB3(MOSI/OC2)), X3.5, X4.5
unnamed: 1N5824.C, IC1.2 (OUT), L1.2
unnamed: LED2.A, R2.1
unnamed: 16MHZ.2, U4.7 (PB6(XTAL1/TOSC1))
unnamed: 16MHZ.1, U4.8 (PB7(XTAL2/TOSC2))
unnamed: MOSFET_60V_12A.3 (D), X2.2
unnamed: R5.2, U1.12 (USBDM)
unnamed: R10.2, U1.11 (USBDP)
unnamed: LED3.A, R6.2
unnamed: LED4.A, R7.2
unnamed: IC3.1 (ADJ), R14.2, R15.1
unnamed: C1.1, JP12.MTN1 (MTN2), JP12.MTN2 (MTN3), JP12.MTN3 (MTN1), JP12.MTN4
PI_5V: 220UF.+, IC1.4 (FB), L1.1, X5.2 (5V0)
PI_RX: R19.1, T2.4 (S), X5.10 (RXD)
PI_SCL: R12.2, T1.4 (S), X5.5 (SCL)
PI_SDA: R1.2, T1.1 (S), X5.3 (SDA)
PI_TX: R18.1, T2.1 (S), X5.8 (TXD)
RESET: C8.2, C11.1, ICSP.5, R3.1, S1.3, S1.4, TP6.P$1, U4.29 (PC6(/RESET))
RX: R8.1, R20.1, T2.6 (D), U4.30 (PD0(RXD))
RXD: R9.2, U1.4 (RXD)
RXLED: LED4.C, U1.17 (CBUS1)
SCK: ICSP.3, TP5.P$1, U4.17 (PB5(SCK)), X3.6, X4.6
SCL: R16.2, T1.3 (D)
SDA: R17.2, T1.6 (D), U4.14 (PB2(SS/OC1B)), X4.7
TX: R9.1, R21.1, T2.3 (D), U4.31 (PD1(TXD))
TXD: R8.2, U1.20 (TXD)
TXLED: LED3.C, U1.10 (CBUS2)
USBVCC: C12.1, C15.+, D1.A, F1.2, U1.15 (VCC)
VIN: C5.+, IC3.3 (IN), J3.VIN0 (PWR), X2.1
VUSB: C10.1, F1.1, JP12.VBUS

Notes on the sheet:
Atmega Power Supply
ATmega_328P-AU
USB To Serial Converter
3.3V 150mA Out
Vin: 12V 5A
RFID 1
RFID 2
SDA
DISPLAY CONNECTOR
SOLENOID LOCK CONNECTOR
1N4001-TP
GND
POS
/RESET
/SDA
Door Security System
GROUP 8 - PROJECT SCHEMATIC
11/1/2020
Level Shifters
Raspberry PI Power Supply
5V/3A step down
Raspberry Pi Connector

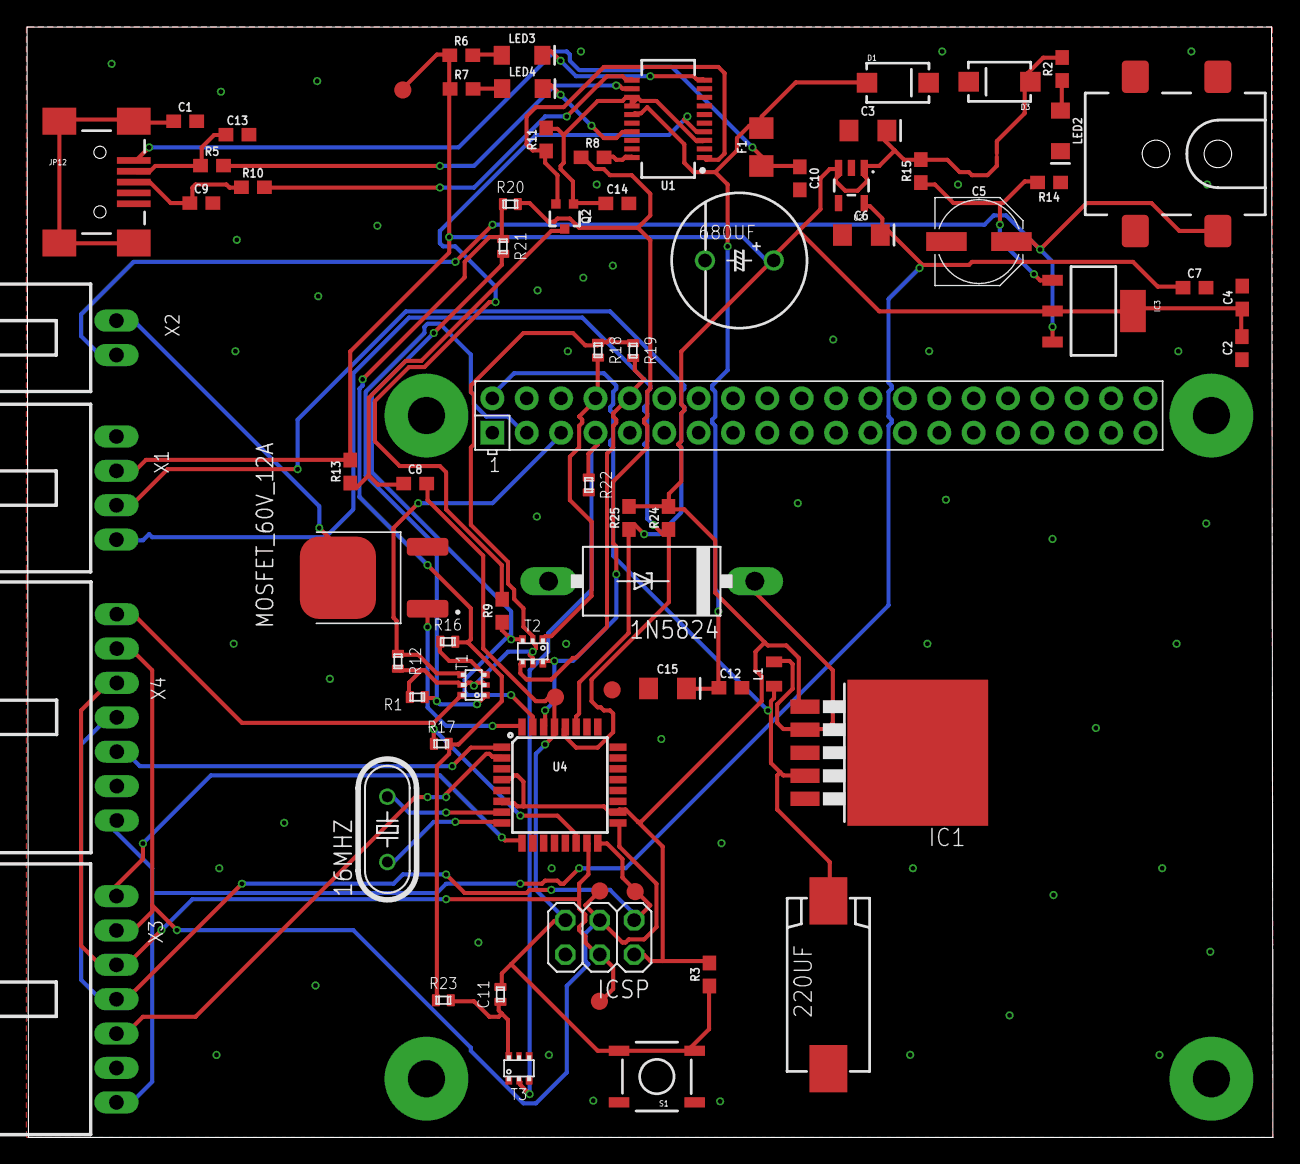
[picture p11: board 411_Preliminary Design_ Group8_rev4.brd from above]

Board: 2 copper layers, 92.1 x 82.0 mm, 75 parts (0 on the bottom side), 49 nets.

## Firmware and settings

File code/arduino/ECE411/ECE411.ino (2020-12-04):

#include <SPI.h>
#include <MFRC522.h>

// lcd
#include <LiquidCrystal_I2C.h>  //http://downloads.arduino.cc/libraries/github.com/marcoschwartz/LiquidCrystal_I2C-1.1.2.zip
#include <Wire.h>               // https://www.resistorpark.com/content/Arduino_Libraries/wire.zip

#define RST_PIN         9          // Configurable, see typical pin layout above
#define SS_1_PIN        10         // Configurable, take a unused pin, only HIGH/LOW required, must be different to SS 2
#define SS_2_PIN        8          // Configurable, take a unused pin, only HIGH/LOW required, must be different to SS 1
#define LED_G         7             //define green LED pin
#define LED_R         6             //define red LED

#define RELAY         2             //relay pin 
#define ACCESS_DELAY 4000
#define DENIED_DELAY 3000

byte ssPins[] = {SS_1_PIN, SS_2_PIN};
MFRC522 mfrc522[RELAY];   // Create MFRC522 instance.
LiquidCrystal_I2C lcd(0x27,20,4);  // set the LCD address to 0x27 for a 16 chars and 2 line display


  
void setup() 
{
  Serial.begin(9600);   // Initiate a serial communication
  while (!Serial);    // Do nothing if no serial port is opened (added for Arduinos based on ATMEGA32U4)
  SPI.begin();          // Initiate  SPI bus
  
  for (uint8_t reader = 0; reader < RELAY; reader++) {
    mfrc522[reader].PCD_Init(ssPins[reader], RST_PIN); // Init each MFRC522 card
    //Serial.print(F("Reader "));
    //Serial.print(reader);
    //Serial.print(F(": "));
    mfrc522[reader].PCD_DumpVersionToSerial();
  }
  
  // Initiate the LCD:
  lcd.init();
  lcd.backlight();
  pinMode(LED_G, OUTPUT);
  pinMode(LED_R, OUTPUT);
  pinMode(RELAY, OUTPUT);
  digitalWrite(RELAY, LOW);
  
    lcd.setCursor(1, 0); 
    lcd.print("Scan Your Face");
    lcd.setCursor(6, 1); 
    lcd.print("^-^");

}


  int counter = 0;
  int DXT = 1;
  int RXT = 0;


void loop() {

  if (DXT ==1){ 
    Serial.write(1);
  }
  
    if (Serial.available() > 0) {
      int DATA = Serial.read() - '0';

      if ( DATA == 1 ){
        Serial.write(RXT);
        lcd.clear();
        lcd.setCursor(1, 0); 
        lcd.print("Scan Your Key"); 

        String content= "";
for (uint8_t reader = 0; reader < RELAY; reader++) {
    // Look for new cards

    if (mfrc522[reader].PICC_IsNewCardPresent() && mfrc522[reader].PICC_ReadCardSerial()) {
      Serial.print(F("Reader "));
      Serial.print(reader);
      MFRC522::PICC_Type piccType = mfrc522[reader].PICC_GetType(mfrc522[reader].uid.sak);
      Serial.println(mfrc522[reader].PICC_GetTypeName(piccType));

      for (byte i = 0; i < mfrc522[reader].uid.size; i++) 
      {
        Serial.print(mfrc522[reader].uid.uidByte[i] < 0x10 ? " 0" : " ");
        Serial.print(mfrc522[reader].uid.uidByte[i], HEX);
        content.concat(String(mfrc522[reader].uid.uidByte[i] < 0x10 ? " 0" : " "));
        content.concat(String(mfrc522[reader].uid.uidByte[i], HEX));
      }
      content.toUpperCase();
      
      
      
      
      
      if (content.substring(1) == "D7 F0 57 B2") //change here the UID of the card/cards that you want to give access
      {
        if (reader == 0){ counter++; }
        if (reader == 1 && counter > 0){ counter--; }
        
        Serial.println("Authorized access");
        Serial.println();
        delay(500);
        lcd.clear();
        lcd.setCursor(0, 0); 
        lcd.print("Access Authoried");  
        lcd.setCursor(6, 1); 
        lcd.print("^-^");
        digitalWrite(RELAY, HIGH);
        digitalWrite(LED_G, HIGH);
        delay(ACCESS_DELAY);
        digitalWrite(RELAY, LOW);
        digitalWrite(LED_G, LOW);

        lcd.clear();
        lcd.setCursor(1, 0); 
        lcd.print("Scan Your Key");
        lcd.setCursor(6, 1); 
        lcd.print("^-^");
        lcd.setCursor(11, 1); 
        lcd.print(counter);
      }
      else   {
        Serial.println("Access denied");
        lcd.print("Access Denied!");  
        lcd.clear();
        lcd.setCursor(1, 0); 
        lcd.print("Acess Denied!");
        lcd.setCursor(6, 1); 
        lcd.print("*-*");
        digitalWrite(LED_R, HIGH);
        delay(DENIED_DELAY);
        digitalWrite(LED_R, LOW);
        lcd.setCursor(1, 0); 
    
        lcd.clear();
        lcd.setCursor(1, 0); 
        lcd.print("Scan Your Key");
        lcd.setCursor(6, 1); 
        lcd.print("^-^");
        }


        
      // Halt PICC
      mfrc522[reader].PICC_HaltA();
      // Stop encryption on PCD
      mfrc522[reader].PCD_StopCrypto1();
    } //if (mfrc522[reader].PICC_IsNewC
  } //for(uint8_t reader


      }
      
      if ( DATA == RXT ){
        lcd.clear();
        lcd.setCursor(1, 0); 
        lcd.print("Scan Your Face"); 
        Serial.write(DXT);
      }

} // serial 


}// LOOP


 /**
 * Helper routine to dump a byte array as hex values to Serial.
 */
void dump_byte_array(byte *buffer, byte bufferSize) {
  for (byte i = 0; i < bufferSize; i++) {
    Serial.print(buffer[i] < 0x10 ? " 0" : " ");
    Serial.print(buffer[i], HEX);
  }
}

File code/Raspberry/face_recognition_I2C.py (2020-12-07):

import numpy as np
import cv2
import time
from smbus import SMBus

addr = 0x8 # bus address
bus = SMBus(1) # indicates /dev/ic2-1


faceDetect = cv2.CascadeClassifier('haarcascade_frontalface_default.xml')

cam = cv2.VideoCapture(0)
rec = cv2.face.LBPHFaceRecognizer_create()
rec.read("recognizer/trainningData.yml")
id = 0
font = cv2.FONT_HERSHEY_SIMPLEX

def solenoid():
       
            # unlock door
            bus.write_byte(addr, 0x1)
            # wait for 5 seconds before locking door
            time.sleep(5)
            #lock the door
            bus.write_byte(addr, 0x0) 
    
while True:
 try:
   ret, img = cam.read()
   gray=cv2.cvtColor(img,cv2.COLOR_BGR2GRAY)
   faces = faceDetect.detectMultiScale(gray,1.3,5)

   for (x,y,w,h) in faces:
       #cv2.rectangle(img, (x,y), (x+w, y+h), (0,0,255), 2)
       id, conf = rec.predict(gray[y:y+h, x:x+w])
       
       
       if id==1:
            id = "josh"
            print('Welcome Josh Pradera! ')
            cam.release()
            cam = cv2.VideoCapture(0)
            solenoid()
        
        elif id!=1:
            print('Unauthorized User! ')
            cam.release()
            cam = cv2.VideoCapture(0)
         
            
       #cv2.putText(img, str(id), (x,y+h),font,3, (255,0,0),1,)

   #cv2.imshow("face", img)
 except KeyboardInterrupt:
   print (' All done... ')
   break

cam.release()
cv2.destroyAllWindows()

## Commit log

2020-11-02 Add files via upload
    First Revision of our Project's schematic
    [411_Preliminary Design_Group8_rev1.sch]
2020-11-02 Add files via upload
    Breadboard setup of our preliminary schematic
2020-11-09 added Preliminary Design Revision 2
    [411_Preliminary Design_Group8_rev2.sch]
2020-11-09 Add files via upload
    Preliminary board layout for PCB, Revision 2
    [411_Preliminary Design_ Group8_rev2.brd]
2020-11-15 Updated PCB
    [411_Preliminary Design_ Group8_rev4.brd, 411_Preliminary Design_ Group8_rev4.sch]
2020-11-19 Update Board Layout and Schematic
    [411_Preliminary Design_ Group8_rev4_5.brd, 411_Preliminary Design_ Group8_rev4_5.sch]
2020-11-19 Updating layout
    [411_Preliminary Design_ Group8_rev4_5.brd]
2020-12-02 Updated BOM Items
    [BOM_Rev3 - Sheet1.csv]
2020-12-04 updated arduino code
2020-12-04 updated Raspberry code
2020-12-04 Add files via upload
    I2C communication Raspberry/Arduino
2020-12-04 Add files via upload
    I2C approach communication Raspberry/Arduino
2020-12-06 Arduino README

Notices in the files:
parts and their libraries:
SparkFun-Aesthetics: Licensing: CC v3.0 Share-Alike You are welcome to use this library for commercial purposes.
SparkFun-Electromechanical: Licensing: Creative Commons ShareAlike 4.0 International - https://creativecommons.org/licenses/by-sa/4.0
